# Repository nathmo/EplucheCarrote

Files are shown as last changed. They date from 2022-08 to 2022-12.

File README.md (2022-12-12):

# EplucheCarrote
crank operated semi automatic carrot peeler

this repo contains :
* material list (BOM in the 200 $ range) (the work hours are not counted, only hardware in unit quantity)
* mechanical 2D schematic
* mathematical and physical modelling
* assembly and usage instruction
* step file + inventor files
* real world demonstration using a 3D printed prototype











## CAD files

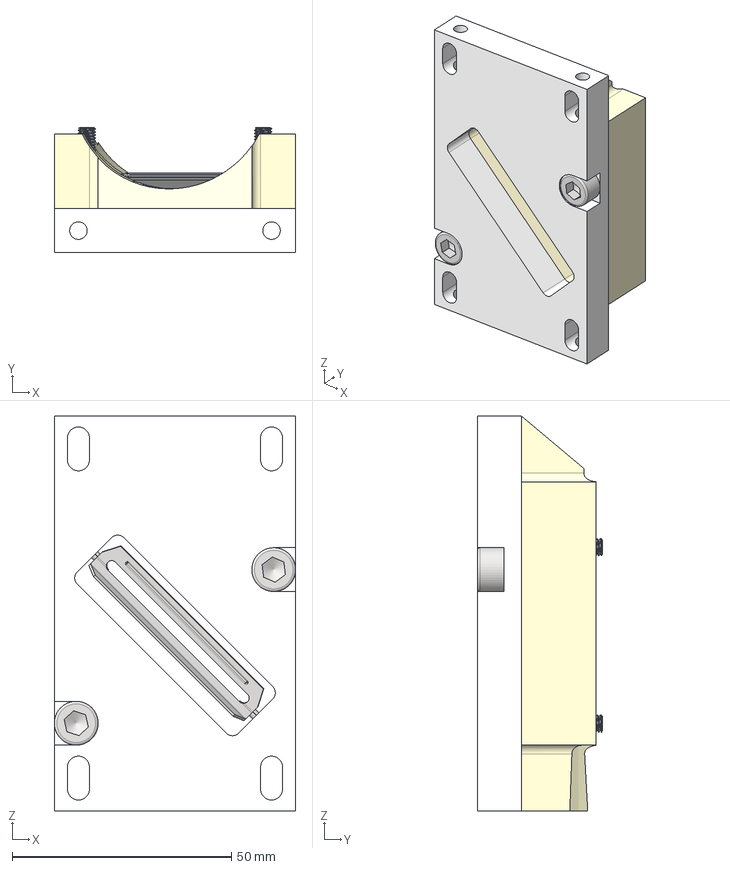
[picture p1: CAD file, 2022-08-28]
STEP/AssemblageStep3Assembled.stp
55.0 x 28.5 x 90.0 mm
92605A528_Stainless Steel Flat-Tip Set Screw x 2
Carrot_Peeler_Blade
GuideCarotte
ISO 4762 - M6 x 12 x 2
SupportGuideCarotte

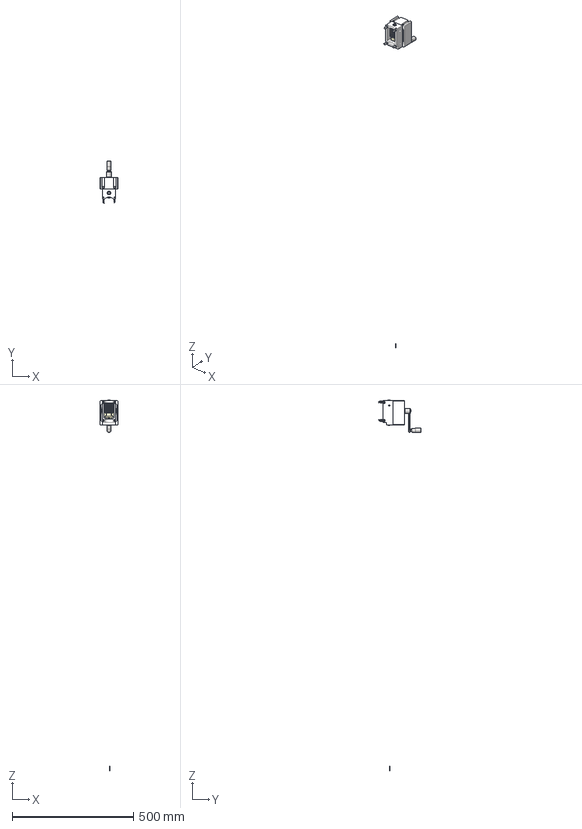
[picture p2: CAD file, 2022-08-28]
STEP/AssemblageStep5Assembled.stp
75.0 x 174.7 x 1527.3 mm
1942N55_Corrosion-Resistant Extension Springs with Hook Ends x 8
2662N415_20DegreePressureAnglePlasticGear
2662N435_20DegreePressureAnglePlasticGear
2810N4_PlasticMiterGear x 2
2977N12_Rounded Machine Key x 2
2977N13_Rounded Machine Key x 2
6545N13_303 Stainless Steel Unthreaded Through-Hole Crank Handle
57785K314_Food Industry Dry-Running Sleeve Bearing x 5
57785K318_Food Industry Dry-Running Sleeve Bearing x 2
93600A531_316 Stainless Steel Dowel Pin x 4
98317A224_Side-Mount External Retaining Ring x 6
AxeHorizontalRoller
AxeVerticalCaptif
AxeVerticalManivelle
CarterEngrennage
CarterRouleau
JointTorique x 8
Roller
ISO 4762 - M6 x 12 x 4

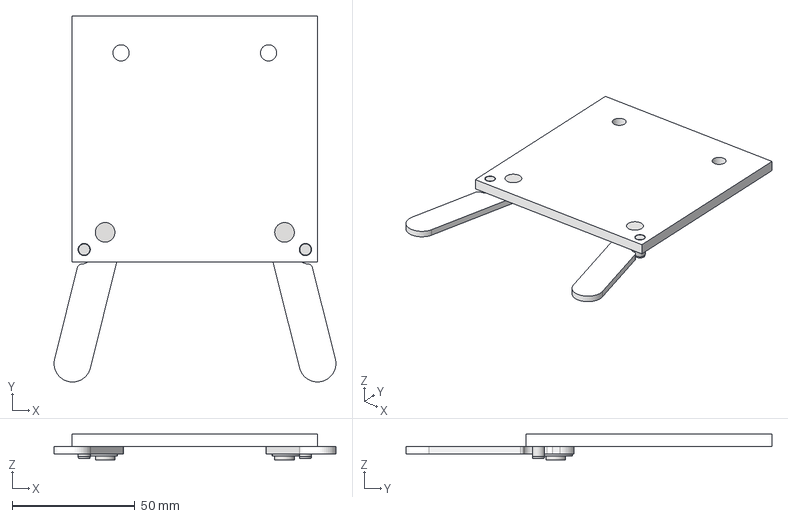
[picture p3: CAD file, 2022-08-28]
STEP/AssemblageStep4Assembled.stp
114.7 x 148.9 x 10.5 mm
93600A511_316 Stainless Steel Dowel Pin x 2
Jambe x 2
AxeJambe x 2
98317A224_Side-Mount External Retaining Ring x 2
PlaqueGuideBlocLame

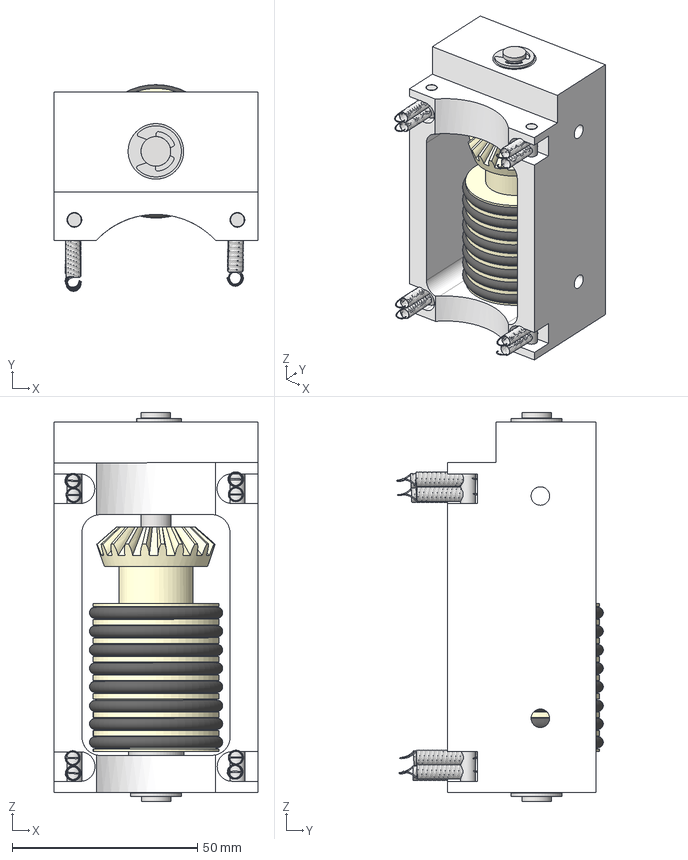
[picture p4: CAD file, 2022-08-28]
STEP/AssemblageStep2Assembled.stp
55.1 x 55.8 x 105.0 mm
1942N55_Corrosion-Resistant Extension Springs with Hook Ends x 8
2810N4_PlasticMiterGear
93600A531_316 Stainless Steel Dowel Pin x 4
98317A224_Side-Mount External Retaining Ring x 2
AxeHorizontalRoller
CarterRouleau
JointTorique x 8
Roller
57785K314_Food Industry Dry-Running Sleeve Bearing x 3
2977N12_Rounded Machine Key x 2

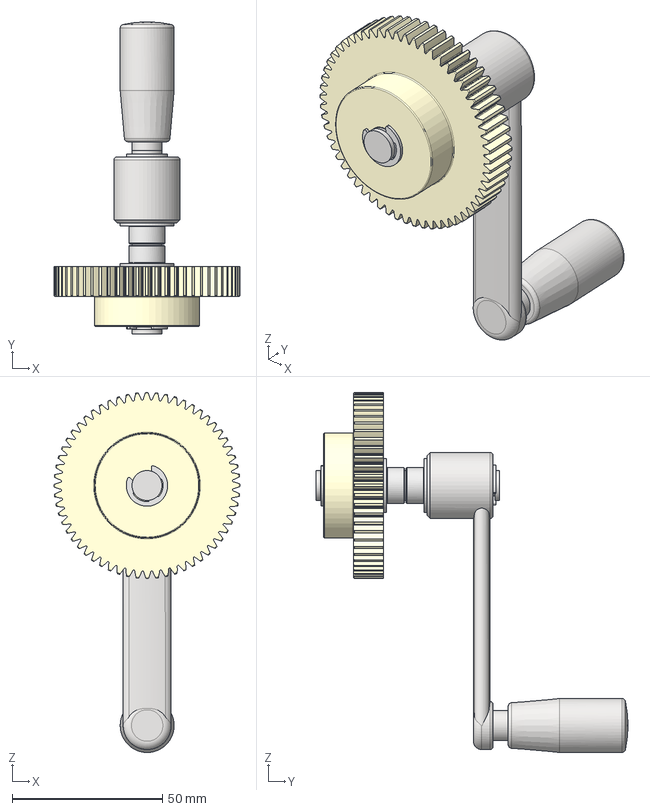
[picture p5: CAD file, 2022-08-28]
STEP/AssemblageStep0AxeManivelle.stp
62.0 x 104.1 x 120.0 mm
2662N435_20DegreePressureAnglePlasticGear
2977N13_Rounded Machine Key x 2
6545N13_303 Stainless Steel Unthreaded Through-Hole Crank Handle
57785K318_Food Industry Dry-Running Sleeve Bearing x 2
AxeVerticalManivelle
98317A224_Side-Mount External Retaining Ring x 2

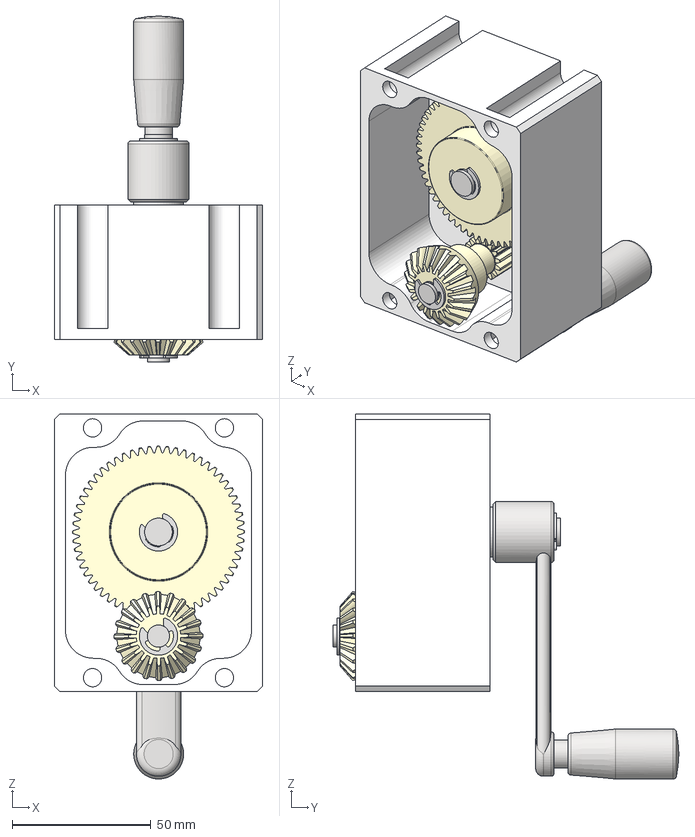
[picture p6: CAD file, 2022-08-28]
STEP/AssemblageStep1Assembled.stp
75.0 x 124.6 x 131.5 mm
2662N415_20DegreePressureAnglePlasticGear
2662N435_20DegreePressureAnglePlasticGear
2977N12_Rounded Machine Key
2977N13_Rounded Machine Key x 2
6545N13_303 Stainless Steel Unthreaded Through-Hole Crank Handle
57785K314_Food Industry Dry-Running Sleeve Bearing x 2
57785K318_Food Industry Dry-Running Sleeve Bearing x 2
AxeVerticalCaptif
AxeVerticalManivelle
CarterEngrennage
2810N4_PlasticMiterGear
98317A224_Side-Mount External Retaining Ring x 4

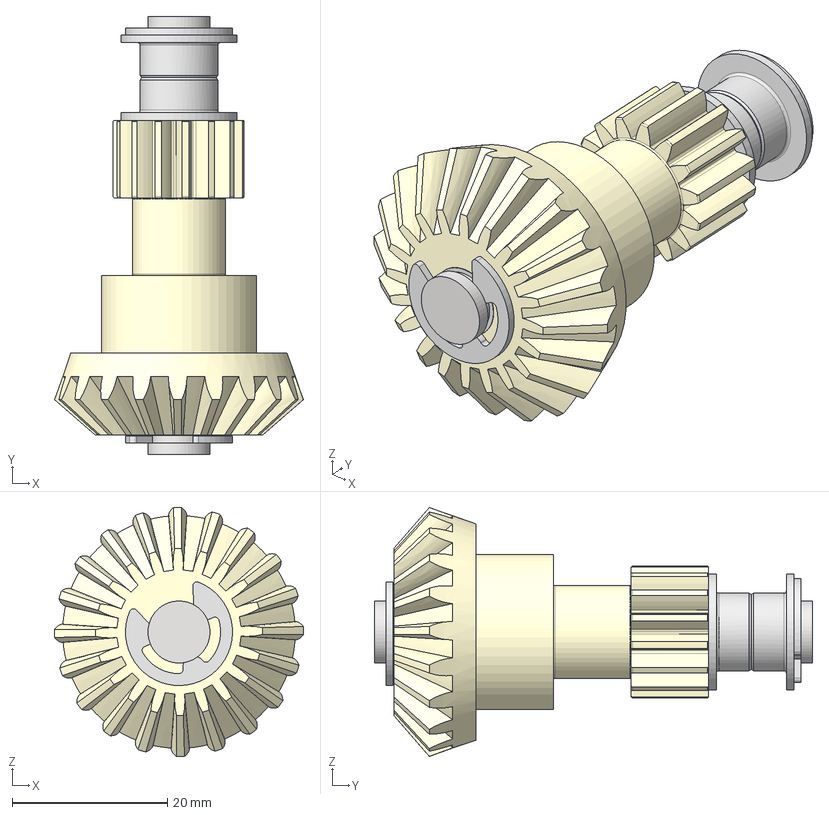
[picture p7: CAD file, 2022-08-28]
STEP/AssemblageStep0AxeCaptif.stp
32.1 x 56.5 x 32.1 mm
2662N415_20DegreePressureAnglePlasticGear
2977N12_Rounded Machine Key
57785K314_Food Industry Dry-Running Sleeve Bearing x 2
AxeVerticalCaptif
2810N4_PlasticMiterGear
98317A224_Side-Mount External Retaining Ring x 2

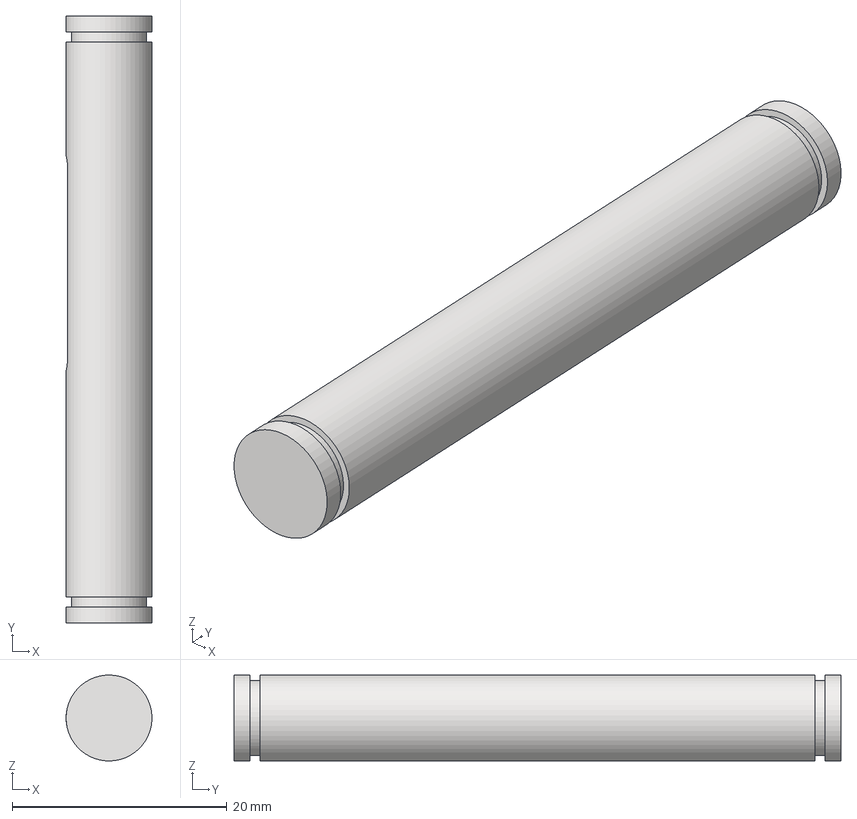
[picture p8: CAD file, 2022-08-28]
STEP/AxeVerticalCaptif.stp
7.99 x 56.5 x 8.00 mm

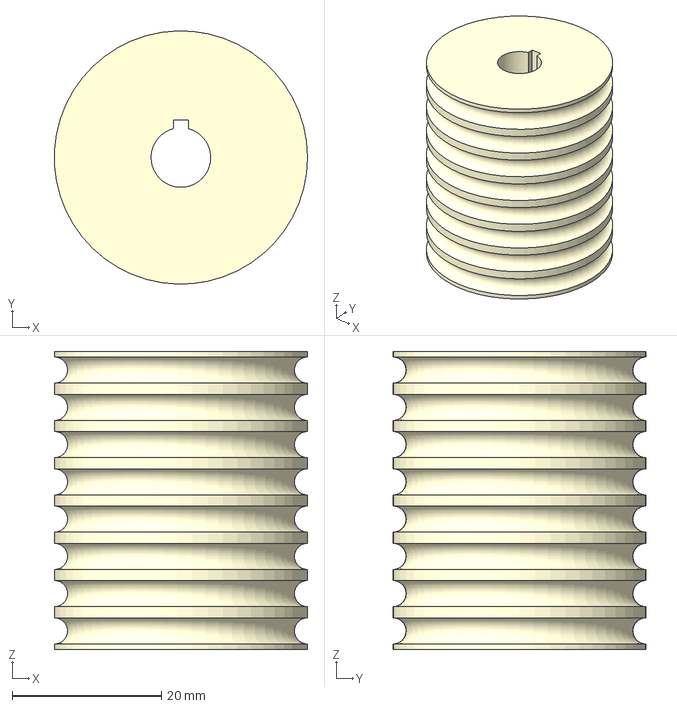
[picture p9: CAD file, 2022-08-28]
STEP/Roller.stp
34.0 x 34.0 x 40.0 mm

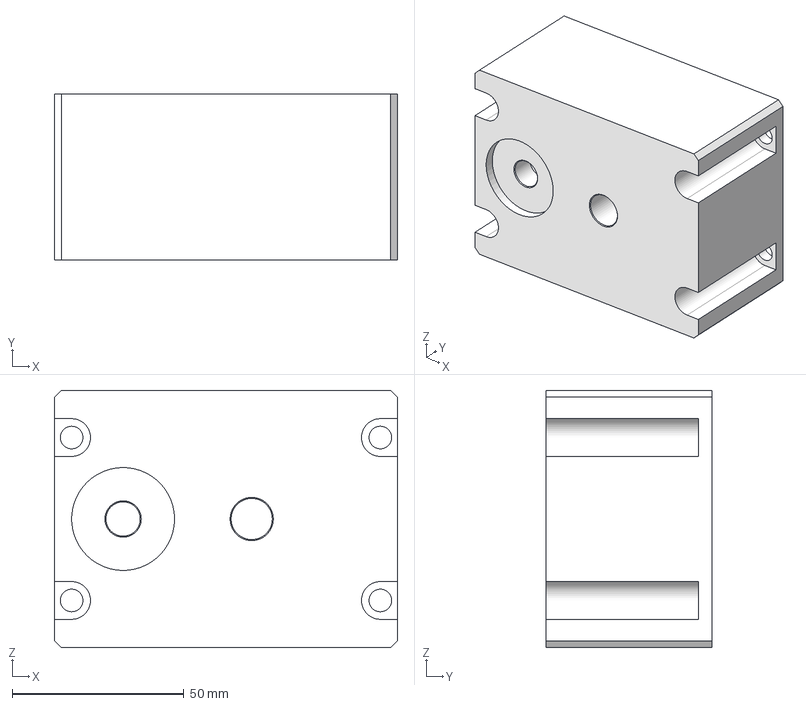
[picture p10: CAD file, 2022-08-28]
STEP/CarterEngrennage.stp
100.0 x 48.5 x 75.0 mm

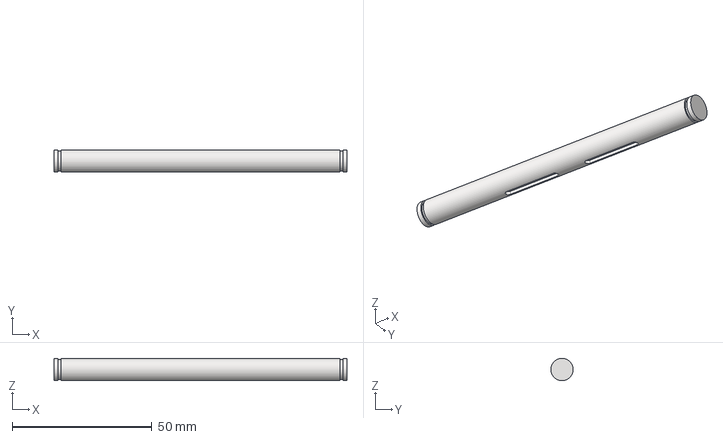
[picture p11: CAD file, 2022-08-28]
STEP/AxeHorizontalRoller.stp
105.0 x 7.99 x 8.00 mm

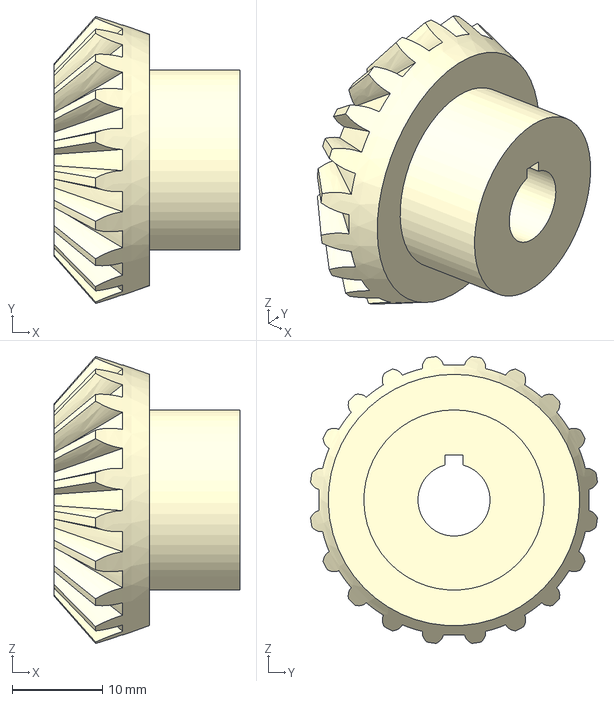
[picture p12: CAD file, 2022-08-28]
STEP/2810N4_PlasticMiterGear.stp
20.6 x 31.9 x 31.9 mm

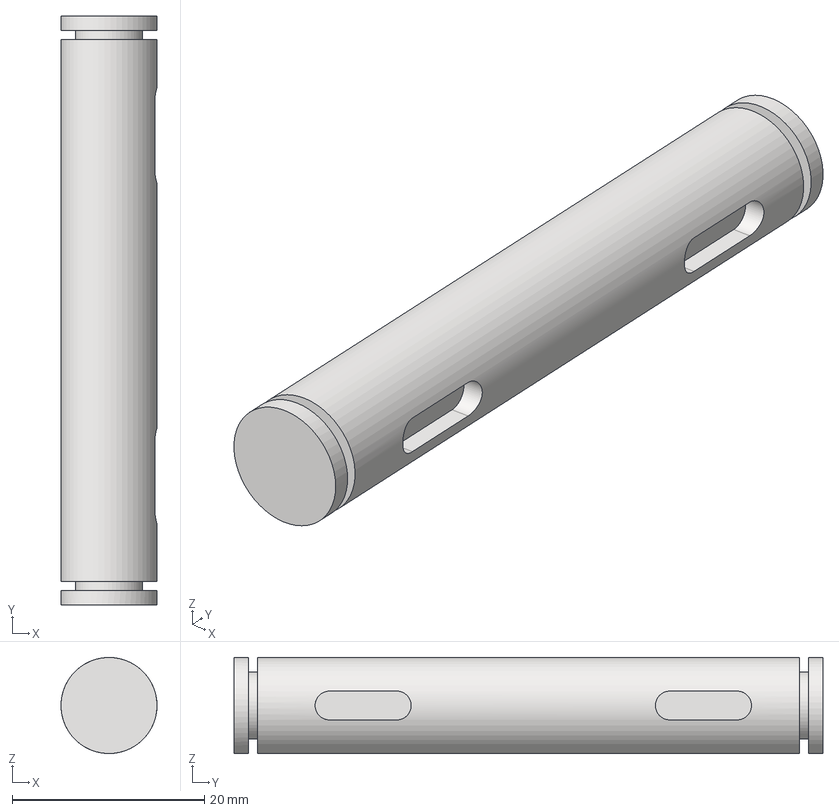
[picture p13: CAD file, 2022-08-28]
STEP/AxeVerticalManivelle.stp
10.0 x 61.3 x 10.0 mm

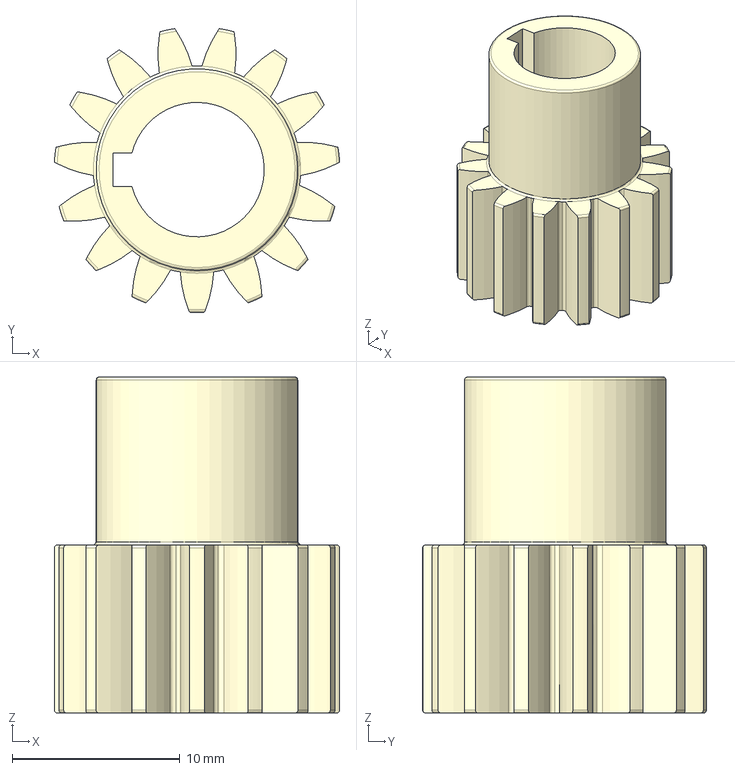
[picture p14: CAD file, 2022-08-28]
STEP/2662N415_20DegreePressureAnglePlasticGear.stp
17.0 x 16.9 x 20.0 mm

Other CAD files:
STEP/2662N435_20DegreePressureAnglePlasticGear.stp
1942N55_Corrosion-Resistant Extension Springs with Hook Ends.ipt
2662N415_20DegreePressureAnglePlasticGear.ipt
2662N435_20DegreePressureAnglePlasticGear.ipt
2810N4_PlasticMiterGear.ipt
2977N12_Rounded Machine Key.ipt
2977N13_Rounded Machine Key.ipt
57785K314_Food Industry Dry-Running Sleeve Bearing-MINOUCHE.ipt
57785K318_Food Industry Dry-Running Sleeve Bearing.ipt
6545N13_303 Stainless Steel Unthreaded Through-Hole Crank Handle.ipt
92605A528_Stainless Steel Flat-Tip Set Screw.ipt
93600A511_316 Stainless Steel Dowel Pin.ipt
93600A531_316 Stainless Steel Dowel Pin.ipt
98317A224_Side-Mount External Retaining Ring.ipt
AssemblyPeleCarotte-SURFACE-NAT-MINOUCHE.iam
AssemblyPeleCarotte-SURFACE-NAT.iam
AssemblyPeleCarotte.CATProduct
AssemblyPeleCarotte/1942N55_Corrosion-Resistant Extension Springs with Hook Ends.CATPart
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

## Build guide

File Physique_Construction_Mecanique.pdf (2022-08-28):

# Physique Construction Mécanique

Avril 2022

Introduction :

Dans ce document, nous allons développer les points théoriques démontrant le bon fonctionnement pèle carotte que nous avons conçu, tant sur le point physique que mécanique.

## 1 Physique

### 1.1 Force pour peler la carotte

Objectif : Déterminer la force à appliquer pour découper la carotte (insertion et découpe). Afin de déterminer ces valeurs,
nous | avons | mesuré | empiriquement | la | force | à | l’aide | d’une | balance | de | cuisine.
Valeurs expérimentales : 5N en moyenne et pic à 10N lors la découpe.

### 1.1.1 Force et vitesse angulaire fournies par un humain

Objectif : Déterminer la puissance que peut fournir l’utilisateur sans se fatiguer afin d’adapter l’ergonomie de l’appareil.

Après lecture de la littérature traitant de physiologie et d’ergonomie, nous avons pu compiler le tableau suivant.

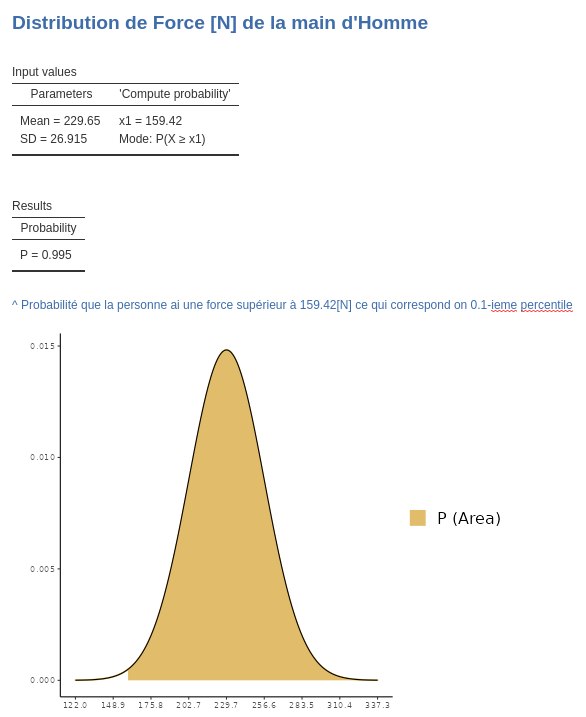
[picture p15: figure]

nous avons la force maximum qu’une personne peut fournir. de là nous avons utilisé cette force et une étude de la NASA sur les capacités du corps humain pour obtenir une courbe à puissance constante tel que les gens ne se fatiguent pas.

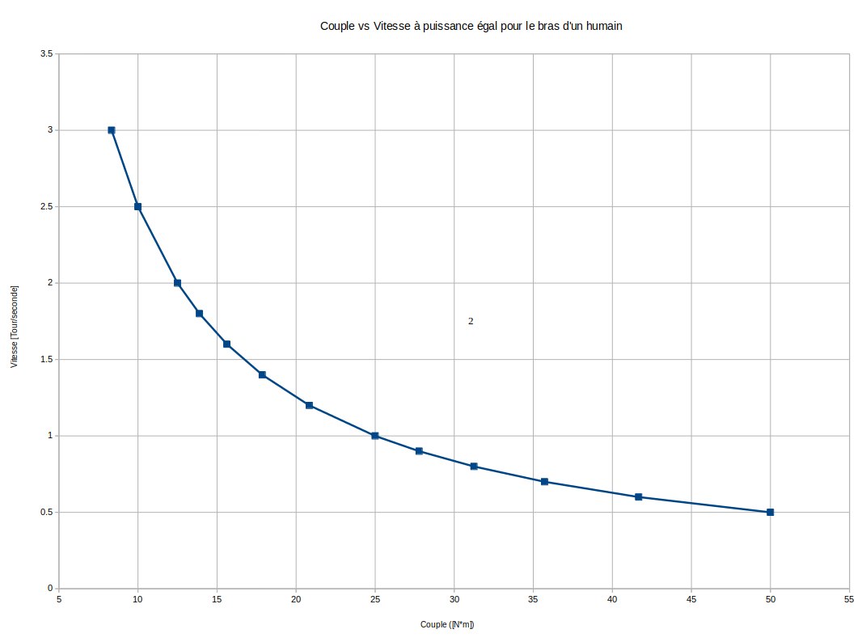
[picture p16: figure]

Celle-ci montre que la quasi-totalité des adultes (homme et femme) sont en mesure de fournir une puissance de 12.5 ± 6.2 [W].

### 1.2 Angle entraînement carotte (ratio avance/rotation)

Objectif : Déterminer le ratio nécessaire pour une découpe entière et uniforme de la carotte.
Pour ce faire, il est nécessaire de déterminer la largeur moyenne des pelures (cf. les mesures en annexes du rapport sur la largeur des pelures).

Lavance = 5[mm]

Ensuite, il nous est nécessaire calculer le chemin parcouru par la lame autour de la carotte.
Nous ferons l’assomption que l’angle entre la roue et l’axe de la carotte est faible et que par conséquent la section de carotte est toujours circulaire.

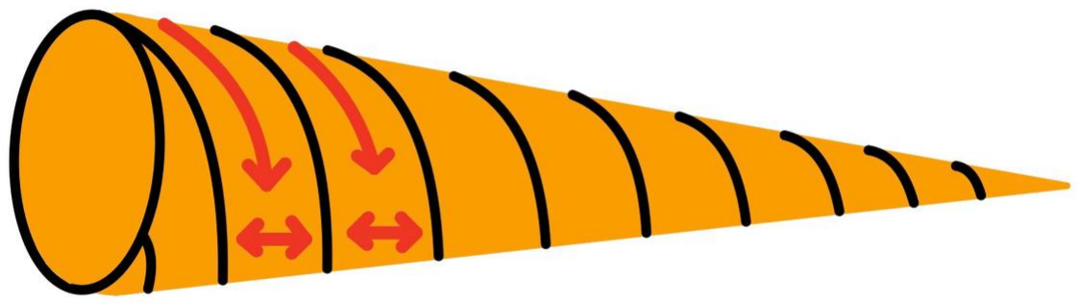
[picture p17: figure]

la figure illustre l’effet de la largeur des pelures lors de d’une pelure hélicoïdale

LperimetreG = 2 ∗ π ∗ R = 2 ∗ π ∗ 22.5[mm] = 141.37[mm]

LperimetreP = 2 ∗ π ∗ R = 2 ∗ π ∗ 10[mm] = 62.83[mm]

Afin d’éviter qu’une partie de la carotte ne soit pas pelée, il est nécessaire de baser ses calculs sur le pire des cas, soit le plus grand rayon.
De par ce choix, certaines zones des carottes de diamètre inférieur à 45mm seront parcourues deux fois par la lame. Cependant, après avoir réalisé des expériences sur ce sujet, nous avons pu conclure que la matière n’est pas retirée lors de la passe supplémentaire.
Il est donc nécessaire de calculer l’angle entre le rouleau et l’axe de la carotte pour garantir une avance le long du périmètre de 141.37 mm alors que l’avance longitudinale doit être de 5 mm.

Voici une figure qui illustre l’angle entre l’axe de la carotte et celui du du rouleau :

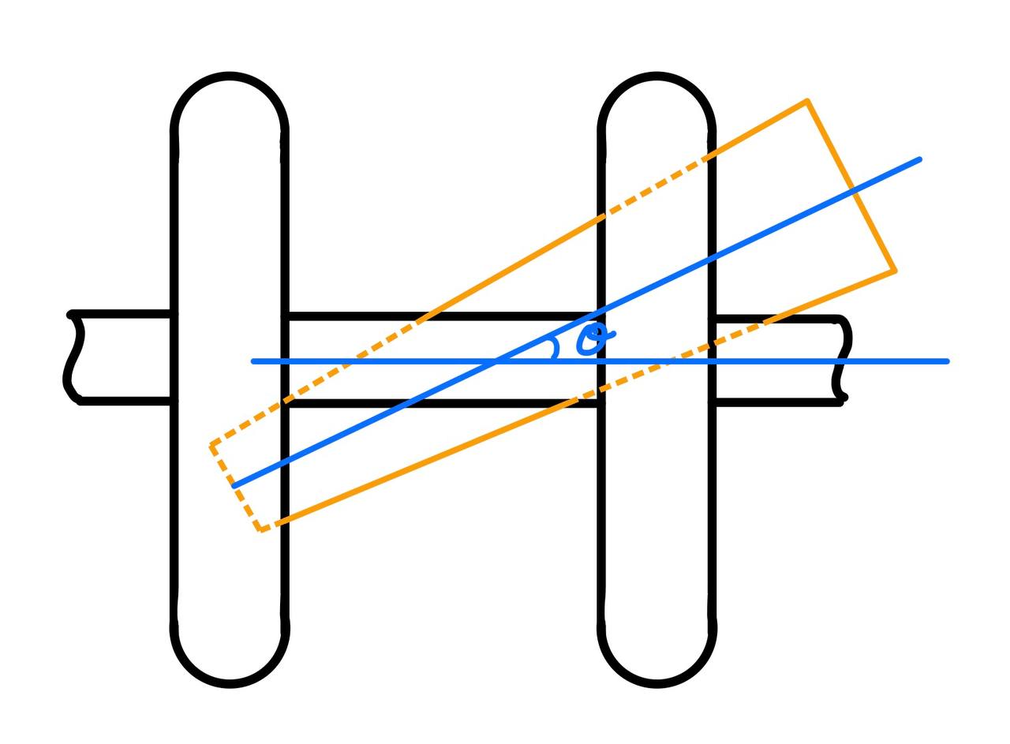
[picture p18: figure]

En utilisant la trigonométrie, on obtient donc :

θ = arctan(

Lavance

LperimetreG

) = arctan(

5[mm]
141.37[mm]

) = 2.03◦

L’angle étant faible, il permet de vérifier l’hypothèse que nous avons effectuée plus tôt quant à la circularité des sections de carotte. Nous pouvons simplifier la pelure hélicoïdale de la carotte comme plusieurs pelures circulaires.

### 1.3 Force de Friction jointe torique/carotte (entraînement et risque de bloquage)

Objectif : Déterminer la valeur minimale de la friction entre la carotte et le rouleau (mu statique, caoutchouc, carotte afin de déterminer le meilleur matériau à utiliser).

Le rouleau doit être en mesure de transmettre un couple supérieur ou égal à celui nécessaire pour découper la carotte [10N] tout en compensant les force de friction de la carotte avec le châssis.
Celles-ci dépendant de la force normale appliquée sur la carotte ainsi que de la force nécessaire pour entraîner la carotte, nous nous retrouvons dans une impasse.
Afin de simplifier le problème, nous allons supposer que les pertes de friction avec le châssis sont négligeables devant la force nécessaire pour peler la carotte, il nous suffira d’ajouter une marge de sécurité, nous allons donc supposer que 20N doivent être transmis à la carotte.

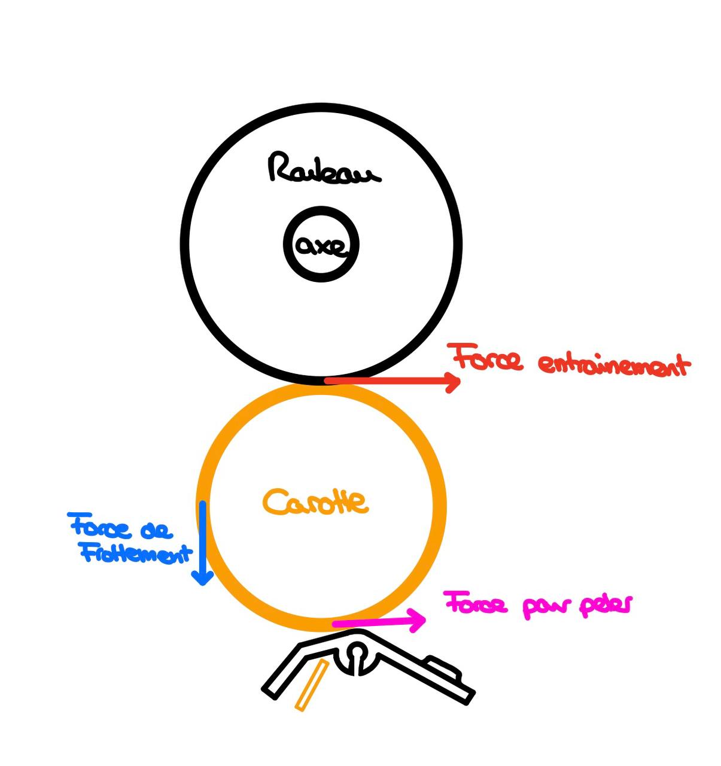
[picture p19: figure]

La force transmise à la carotte dépendant des frottements entre la carotte et les joints toriques du rouleau supposerons que le coefficient de frottements statiques entre la carotte et un joint torique est plus important que celui entre une carotte et de l’acier. Ceci est confirmé par une mesure expérimentale des frottements statiques entre une carotte et un élastomère générique
µd ≈ 0.8

FN =

Ftangent

µstatique

=

20[N]
0.8

= 25[N]

Nous pouvons donc conclure que le mécanisme ne risque pas de se bloquer ni de glisser.

### 1.4 Force normale appliquée par les ressorts

Objectif : Déterminer la constante de raideur des ressorts ainsi que la variation de force normale pour les différentes tailles de carotte possibles.
La force normale ayant été estimée dans le point précédent, nous avons donc dû sélectionner un ressort adapté en fonction de ce que propose le fournisseur. Le ressort est là pour ramener la partie inférieure du boitier et ainsi avoir une force normale sur la carotte en plus de permettre au mécanisme de s’adapter aux irrégularités et forme de carotte. Le choix étant limité, la seule configuration acceptable trouvée contient huit ressorts avec les caractéristiques suivent :

Propriétés du ressort : (Données du fournisseur)

- Longueur au repos : 20.2 mm
- Constante de raideur : 0.04 lbs.mm⁻¹ ⇔ 177.92N.m⁻¹

Ainsi après un processus itératif nous avons fixer la distance minimale sur notre appareil à 35mm :

|FR| = k ∗ (l − l0) = 177.92[N.m⁻¹

] ∗ (35 − 20) ∗ 10⁻³
[m] = 2.66[N]

Cette force est la force minimale appliquée par un seul ressort, nos ressorts étant disposés en parallèle, les forces s’additionnent, ainsi :
FT = 8 ∗ FR[N] = 21.35[N]

Pour la plus grosse carotte cette force atteint :

|FT | = 8 ∗ k ∗ (l − l0) = 8 ∗ 177.92[N.m⁻¹

] ∗ (60 − 20) ∗ 10⁻³
[m] = 56.6[N]

Nous pouvons constater que la force normale est généralement suffisante et que les régions de fonctionnement ou celle-ci est inférieure à la force nécessaire sont aussi celles ou les frottements seront les plus faibles et donc inférieur au 10 [N] assumé précédemment.

### 1.5 Calcul des pertes dues à la frictions

Objectif : Déterminer les frottement maximum possible entre la carotte et le support dans le pire cas et ainsi limiter la gamme de matériaux utilisables pour la surface en contact avec la carotte en fonction des frottements entre les deux surfaces.

FF rottement = FnormalMAX[N] ∗ µP T F E = 56.6[N] ∗ 0.182 = 10.31[N]

pour référence les frottement minimum s’élèvent à

FF rottement = FnormalM IN [N] ∗ µP T F E = 21.35[N] ∗ 0.182 = 3.9[N]

L’assomption faite que la forces d’entraînement minimal de 21.35 N suffise tiens. La force d’entraînement maximal avec les frottement maximal fonctionne aussi.
à partir de ces donner nous pouvons faire le ration des force utile sur le total des forces et ainsi avoir le rendemement (la virtesse de rotation étant la même, les puissance dépendente seulement des forces) :

le pire cas

η =

Fpelage[N]

FnormalMAX[N] ∗ µP OM + Fpelage[N]

∗ ηengrennages =

5[N]
15.31[N]

∗ 0.96 = 0.32

le meilleure cas
η =

Fpelage[N]

FnormalMAX[N] ∗ µP OM + Fpelage[N]

∗ ηengrennages =

5[N]
8.9[N]

∗ 0.96 = 0.54

### 1.6 Stabilité de la carotte et garantie de la découpe ainsi que risque de blocage

Objectif : Garantir la stabilité de la carotte lors de la découpe, ainsi que la stabilité malgré les forces tangentielles appliquées.

### 1.6.1 Position de la lame

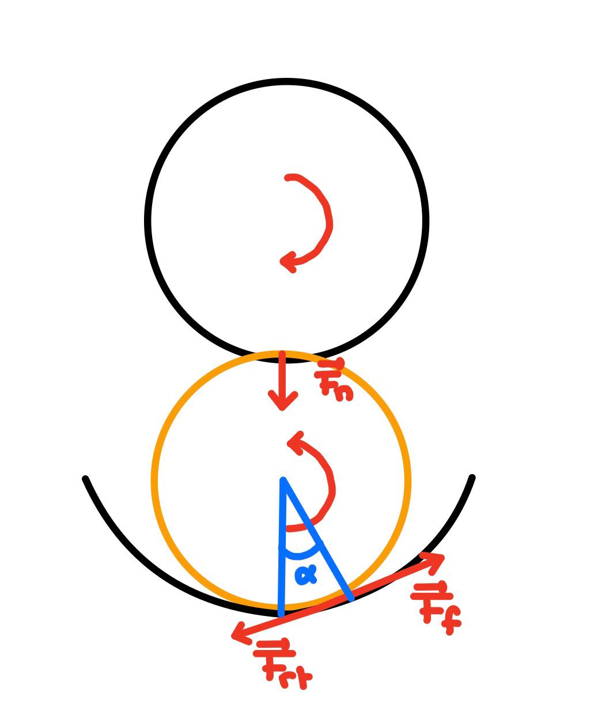
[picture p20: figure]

La lame est située environ trois millimètres au dessus du support de la carotte, la lame est capable de tourner afin de s’adapter aux légères inconsistances dans la taille de la carotte.

### 1.6.2 Calcul des forces appliquées

Nous avons donc trois forces s’appliquant sur notre carotte :

- Force Tangentielle de la roue : F⃗
T
- Force Normale de réaction de la roue : F⃗N
- Les forces de frottements : F⃗
F

Ainsi :

FT = µCarroteElastomere ∗ FN

FF = µCarroteP OM ∗ FN ∗ cos(α)

P = −m ∗ g

FN = −FRessorts = k ∗ r

D’après la seconde loi de Newton, à l’équilibre : ΣF⃗
ext = 0

FT = FF ⇒ µCarroteP OM ∗ FN ∗ cos(α) = FN ∗ sin(α)

α = arctan(µCarotte/P OM ) = 12.33◦

Ainsi la hauteur de déviation s’exprime :

hDEV = RR(1 − cos(α)) = 40 ∗ 10⁻³

(1 − cos(12.33)) = 9.23 ∗ 10⁻⁴

[m] < 3 ∗ 10⁻³ = hLAME

### 1.6.3 Conclusion

Cette déviation est plus faible en réalité, les ressorts s’adaptant et n’appliquant pas des forces uniquement perpendiculaire à la force tangentielle.
Etant plus faible que la hauteur de la lame, l’influence sur la découpe sera minime. De plus pour ce qui est du blocage, il ´ n’y as pas de risque le système pouvant glisser si il devait être bloqué mais comme démontrer dans les sections précédente, cela ne devrais pas arriver dans le cas d’une utilisation normale.

## 2 Engrenages et systèmes de transmission

### 2.1 Exigences rotation engrenages

Objectif : Définir la taille de la manivelle et ratios d’engrenages a partir des la force nécessaire pour peler tout en restant confortable pour l’utilisateur
Dans le but de garantir un fonctionnement facile à tous les utilisateurs il est nécessaire tenir compte de la force et la vitesse à laquelle un humain peux tourner une manivelle confortablement. De plus il est nécessaire de minimiser la durée d’actionnement pour peler une carotte afin que la tâche ne soit pas épuisante ou pénible.
Après consultation de la littérature, nous en sommes venus à la conclusion que la majorité des adultes (hommes et femmes) peuvent confortablement appliquer une force entre 10 et 20 Newton autour un cercle de rayon compris entre 100 mm et 200 mm à une vitesse d’environ 1 tour/s.
A partir de ces données nous pouvons calculer la puissance pouvant être développée celle-ci est donnée par : `

P = R ∗ F ∗ ω

Où :

- R est le rayon de la manivelle
- F la force tangentielle appliquée par l’utilisateur
- ω est la vitesse angulaire de la manivelle

et est comprise entre 12.5 W ± 6.2 W
Nous pouvons donc calculer l’énergie nécessaire pour peler une carotte en considérant la largeur moyenne de la pelure ainsi que la surface de la carotte et la force nécessaire pour la peler.

E =

S
l

∗ Fpelure

Où :

- S est la surface extérieure de la carotte
- Fpelure est la force nécessaire pour peler la carotte
- l est la largeur de la pelure

Pour la plus petite carotte cette énergie est de 12.56 J Pour la plus grande carotte cette énergie est de 28.27 J
Nous pouvons estimer le temps nécessaire pour couper une carotte comme étant compris entre 1 et 3 secondes selon la taille de la carotte. Mais les pertes vont rallonger ce temps. ainsi en prennant en compte l’éfficacité nous avons un temps comprise entre 2 et 9 secondes.
Le temps de coupe étant fixé et connaissant le couple nécessaire pour peler une carotte nous pouvons déterminer la vitesse de rotation optimale de la carotte (diamètre moyen de la carotte, puissance moyenne fournie par l’utilisateur)

ω =

P
F ∗ l

=

12.5W
5N ∗ 0.0325m

= 76.9rad/s = 12.2tour/s

Sachant que le plus gros rapport d’engrenages disponible à un prix raisonnable est de 1:4 et que le ratio entre les diamètre de la carotte et du rouleau est d’environ 1:1 (l’encombrement d’un rouleau apportant un ratio légèrement meilleur n’est pas justifié), L’utilisateur devra tourner la manivelle à 3 tours par seconde. Or nous savons que que celui-ci n’est capable que de 1 tours par seconde ce qui triple le temps nécessaire et limite la puissance maximale qu’il est possible d’extraire de l’utilisateur .

Ceci triple le temps moyen nécessaire pour peler une carotte mais en moyenne celui-ci reste encore raisonnable meme avec le mauvais rendement et ne justifie pas de rajouter un étage d’engrenage (un de nos objectifs principaux et d’avoir un objet compact et léger).

La force que l’utilisateur doit appliquer sur la manivelle est donnée par la formule suivante:

FT = K ∗ η ∗ FA ∗

L
R
Où:
- FT est la force de l’utilisateur
- K = 4 est le ratio des engrenages

- η = 0.98 est le rendement de la transmission entre engrenages
- FT est la force totale appliquée
- L est la longueur de la manivelle
- R est le rayon du rouleau

Via l’application numérique, nous pouvons constater qu’avec le diamètre de manivelle choisi (qui est compris dans les 100-200mm assumés précédemment) la force est de X Newton qui est égale a la force qu’un humain peut fournir confortablement.

### 2.1.1 Module des roues dentées

Objectif : Calculer le module minimal des roues dentées afin que celles-ci résistent aux contraintes appliquées par la réaction de la carotte
Premièrement il est nécessaire de déterminer la force tangentielle maximum sur la roue dentée au rayon le plus faible.

Le rayon de notre rouleau est de 17 mm.
Le rayon primitif de la plus petite roue est de 7 mm, la force tangentielle maximale sur le rouleau est de 20[N] (10N pour la carotte + une marge pour les perte).
les pertes dues aux engrenages sont considéré comme négligeable et seront donc ignoré ici.

En se basant sur les données de la section 2.1.1 nous pouvons obtenir le couple sur l’axe du rouleau :

| CR = FT ∗ RR = 20[N] ∗ 0.017[m] = 0.34[Nm]

De là on peut poser la force tangentielle sur la petite roue denté car elle ne change pas le couple:

| FTD = CR RD = 0.34[Nm] 0.007[m] = 48.6[N]

en appliquant la formule suivante qui indique si le module est suffisant

| m ≥ 2.34 ∗

s
| T k ∗ σpe

avec :

- T =Force tangentielle = 48.6 [N]
- k = longeur de la dent * surface de la dent (module) = 10[mm]*1
- σpe= resistance du nylon = 30 [MPa]

m ≥ 2.34 ∗

s
48.6[N]
10 ∗ 30[MP a]

= 0.941

cette valeur est la même pour la grande roues denté car les forces tangentielle, matériaux et largeurs de dents sont identiques. Ainsi le module de nos dents doit être de 1 au minimum
Pour ce qui est du module des dents des engrenages coniques, 1 fonctionne aussi car il ont une force tangentielle plus faible du fait de leurs rayon plus grand et de de la plus grande largeur de dents que la petites roue dentée.

### 2.1.2 Force appliquée sur les axes

Objectif : Trouver les forces axiales et radiales s’appliquant sur les axes afin d’adapter les spécifications des roulements et des circlips.

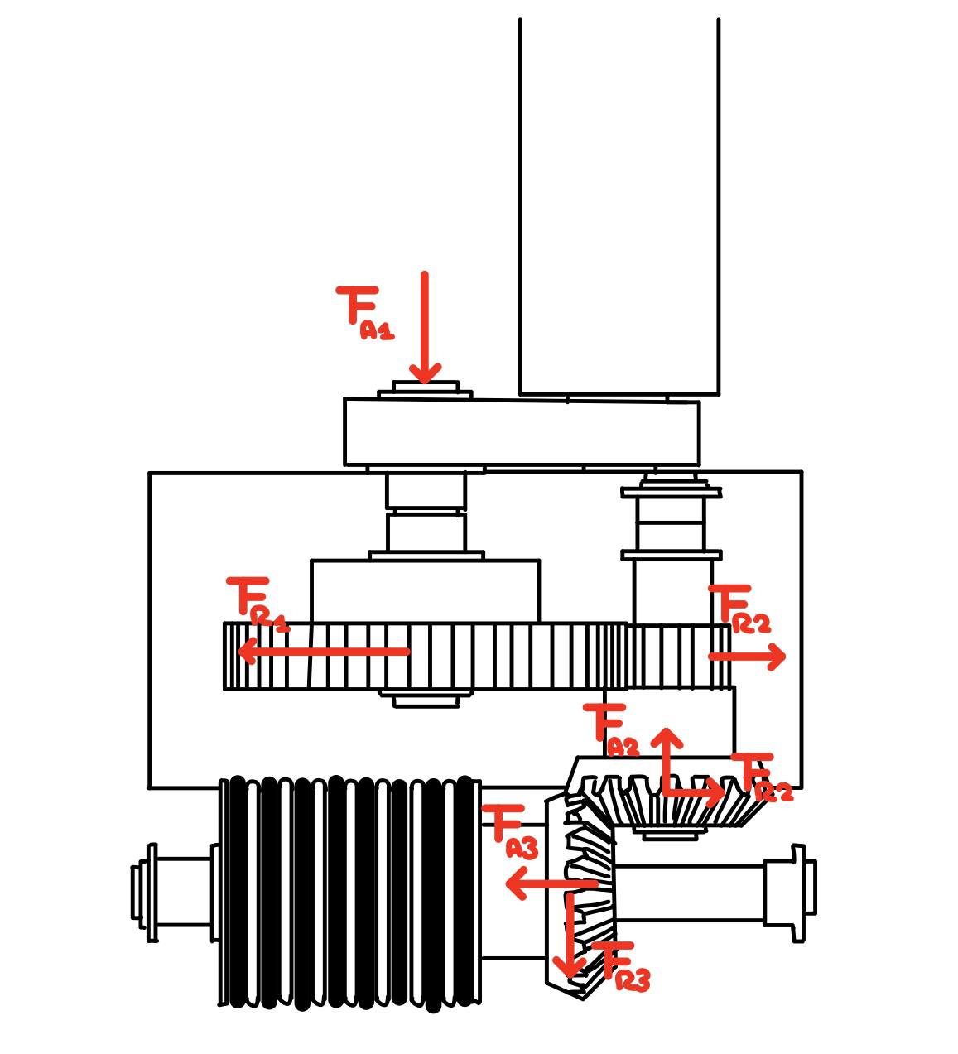
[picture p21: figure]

Comme vu précédemment, nous savons que la force tangentielle appliquée au niveau du rouleau est de 20N.
ainsi nous pouvons calculer le couple sur chaque axe et donc la force tangentiel au niveau des engrenages. de la nous pouvons projeter la parts des forces qui s’applique radialement ou axialement grâce à l’angle de pression des dents et l’angle de 45° des roues coniques.
les pertes dues aux engrenages sont considéré comme négligeable et seront donc ignoré ici.
Données numériques :
- RR, Rayon du rouleau = 17mm
- RC Rayon moyen roues coniques = 15mm
- RD Rayon petite roue droite = 7mm
- RGD Rayon grande roue droite = 30mm
- FT Force tangentielle appliqué par le rouleau = 20N
- α angle de pression des dents = 20◦
- β angle des roues coniques = 45◦

En se basant sur les données de la section 2.1.1 nous pouvons obtenir le couple sur l’axe du rouleau :

CR = FT ∗ RR = 20[N] ∗ 0.017[m] = 0.34[Nm]

De là on peut poser la force tangentielle sur les roues:

FT C =

CR
RC

=

0.34[Nm]
0.015[m]

= 22.7[N]

FTD =

CR
RD

=

0.34[Nm]
0.007[m]

= 48.7[N]

la force tangentielle sur la petite et la grande roues sont les mêmes

FT GD = FTD = 48.7[N]

Ainsi nous pouvons projeter ces forces avec les angles de pression:

- FR1 = FT GD ∗ sin(α) = 48.7[N] ∗ sin(20) = 16.7[N]
- FR2A = FTD ∗ sin(α) = 48.7[N] ∗ sin(20) = 16.7[N]
- FR2B = FT C ∗ sin(α) ∗ sin(β) = 22.7 ∗ sin(20) ∗ sin(45) = 4[N]
- FR3 = FT C ∗ sin(α) ∗ sin(β) = 22.7 ∗ sin(20) ∗ sin(45) = 4[N]
- FA2 = FT C ∗ sin(α) ∗ sin(β) = 22.7 ∗ sin(20) ∗ sin(45) = 4[N]
- FA3 = FT C ∗ sin(α) ∗ sin(β) = 22.7 ∗ sin(20) ∗ sin(45) = 4[N]

Ainsi nous pouvons sommer ces forces et vérifier qu’elle sont inférieur au valeurs maximum admissible pour les pallier lisse et les circlips :
Données du fabriquant :
- Palier lisse de 8mm
Dynamic Radial Load Capacity 60lbs.@120rpm = 266.88[N] Dynamic Thrust Load Capacity 85lbs.@120rpm = 378.08[N]
- Palier lisse de 10mm
Dynamic Radial Load Capacity 75lbs.@120rpm = 333.5[N]
Dynamic Thrust Load Capacity 100lbs.@120rpm = 444.8[N]

La résistance des circlip étant supérieur à celle des paliers lisses ils nous suffit de vérifier les paliers lisses.

Vérification des forces sur les axes :
Radial Load Capacity
- FR1 = 16.7[N] < 333.5[N]
- FR2 = FR2A + FR2B = 33.3[N] < 266.88[N]
- FR3 = 4[N] < 266.88[N]

Dynamic Thrust Load Capacity

- FA1 =Force appliquée par l’utilisateur < 444.8[N]
- FA2 = 4[N] < 333.5[N]
- FA3 = 4[N] < 333.5[N]

la résistance des segments d’arret est de l’ordre 6200 N. la résistance des axes étant au moins égal a la résistance des segment d’arret (car ceux-ci prennent en compte la résistance de l’axe) il vas de soit qu’il n’y as pas de risque de tordre l’axe Conclusion Les pallier lisse et les circlips peuvent donc largement soutenir les forces auxquelles ils sont soumis.

## 3 Dimensionnement des éléments d’assemblage

### 3.1 Vis

Objectif : Déterminer la taille de vis nécessaire à un assemblage stable en évitant le desserrage.
Nous avons décidé de limiter le nombre de vis différentes pour simplifier l’assemblage. De plus la limite de taille de vis arbitraire du cahier des charges impose un diamètre minimal M4 qui est nettement supérieur a ce qui est nécessaire. Nous allons donc prouver que la résistance de la vis M6 est suffisante. Nous avons choisi cette taille de vis afin de faciliter l’assemblage, en plus d’offrir une grande surface sous la tête de vis pour limiter la compression des alliages légers et éviter l’utilisation de rondelle.

### 3.1.1 Longueur d’implantation

La longueur d’implantation minimum est de 6mm, cette longueur est suffisante car les vis ne subissent aucune contrainte et servent uniquement é l’assemblage.

### 3.1.2 Force maximale supportée

Nous avons choisi des vis ayant pour classe de qualité 4.6 ainsi leur résistance élastique est de 240MPa nous pouvons considérer la surface de prise comme la surface d’un cylindre de rayon de 6 mm:

S = 2 ∗ π ∗ r ∗ h = 1.1309 ∗ 10⁻⁴ [m²
]

Ainsi la force maximale que la vis peut supporter en régime élastique

FMAX = PMAX ∗ S = 2.4 ∗ 10⁸

∗ 1.1309 ∗ 10⁻⁴ = 27 ∗ 10³ [N]

La vis peut donc supporter une force bien supérieure à celles qu’elle peut rencontrer lors de l’utilisation de notre machine, notamment les chutes.

### 3.2 Goupilles

Objectif : Déterminer que le dimensionnement et les caractéristiques des goupilles utilisées sont suffisantes pour l’utilisation faite dans le projet.

### 3.2.1 Force maximale supportée

Notre goupille est faite en acier inoxydable (Re = 225[MP a] ⇒ Reg = 117.5[MP a]). Ainsi nous pouvons déterminer la force maximale supportée dans la condition τ = Reg

FMAX = A ∗ Reg

Nous supposons que la section cisaillée correspond à l’aire extérieure de notre goupille (r = 2.5[mm] h = 10[mm]) Ainsi :
A = 2 ∗ π ∗ r ∗ h = 1.57 ∗ 10⁻⁴ [m²
]

FMAX = 117.5 ∗ 10⁶

∗ 1.57 ∗ 10⁻⁴ = 18.5 ∗ 10³ [N]

Nos goupilles supportent donc des forces de 18.5 kN en cisaillement ce qui est largement supérieur à celles qu’elles pourraient rencontrer dans une utilisation normale de l’appareil.
Les composants en rapport avec les axes sont vérifié dans la section précédente.
